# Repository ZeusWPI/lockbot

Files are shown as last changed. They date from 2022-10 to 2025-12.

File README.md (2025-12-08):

# Lockbot

Lockbot is a robot attached to our door that makes it possible for trusted members who don't have a key to open the door. It consists of a servo motor, two gears, a potentiometer and an Arduino Uno + ethernet shield.

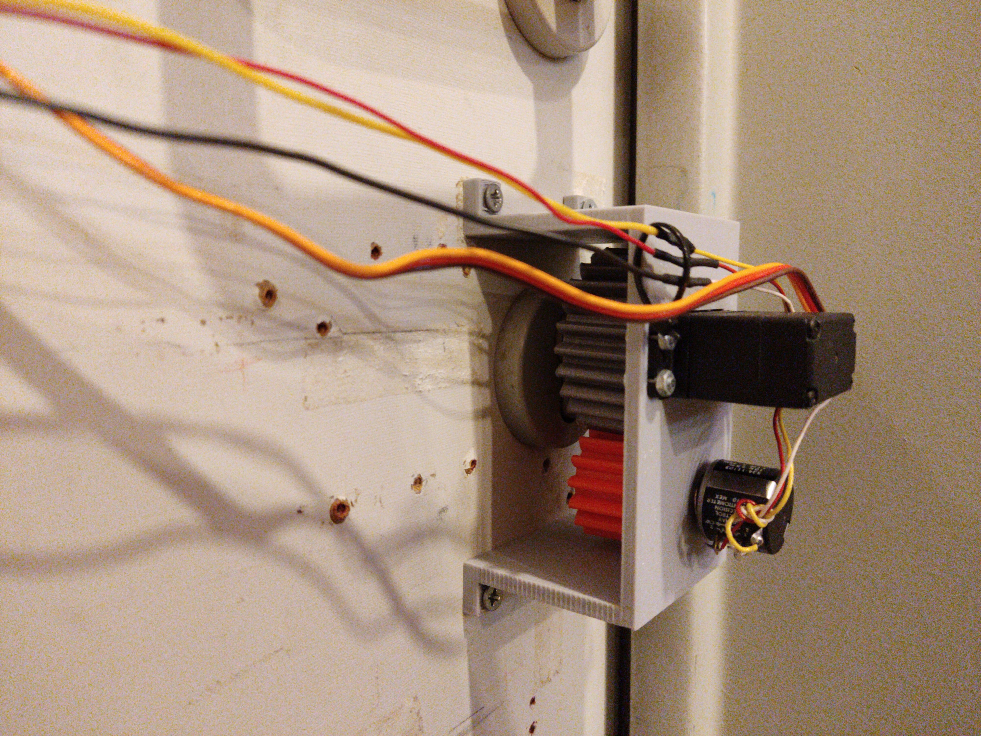
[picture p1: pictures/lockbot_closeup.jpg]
A closeup of just the motor and gears


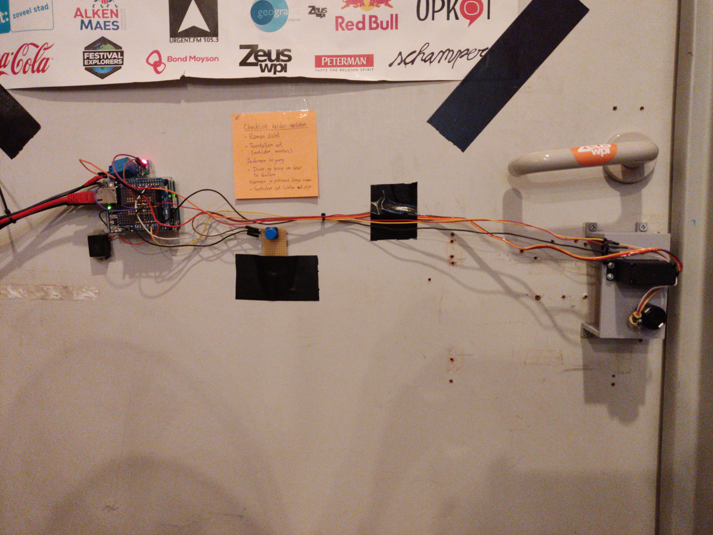
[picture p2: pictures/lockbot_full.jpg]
Global picture of lockbot


## Microcontroller build instructions

Requires the `platformio` cli tool, follow [these instructions](https://docs.platformio.org/en/latest/core/installation/methods/installer-script.html) to install it.

Next, in [arduino/src](arduino/src), copy `tokens.h.example` to `tokens.h` and edit them if necessary.

Finally, in [arduino](arduino), build and flash using the following:
```sh
. ~/.platformio/penv/bin/activate # Might depend on platform
pio run -t clean
pio run
pio run -t upload -t monitor
```

## 3D-print instructions

1. Install OpenSCAD
2. To print each lockbot part, open `printfile.scad` in OpenSCAD, uncomment the part you want to print, render it, export as STL then 3D print it. The big gear should be printed with 5 perimeter walls and solid infill, so it can handle the forces.

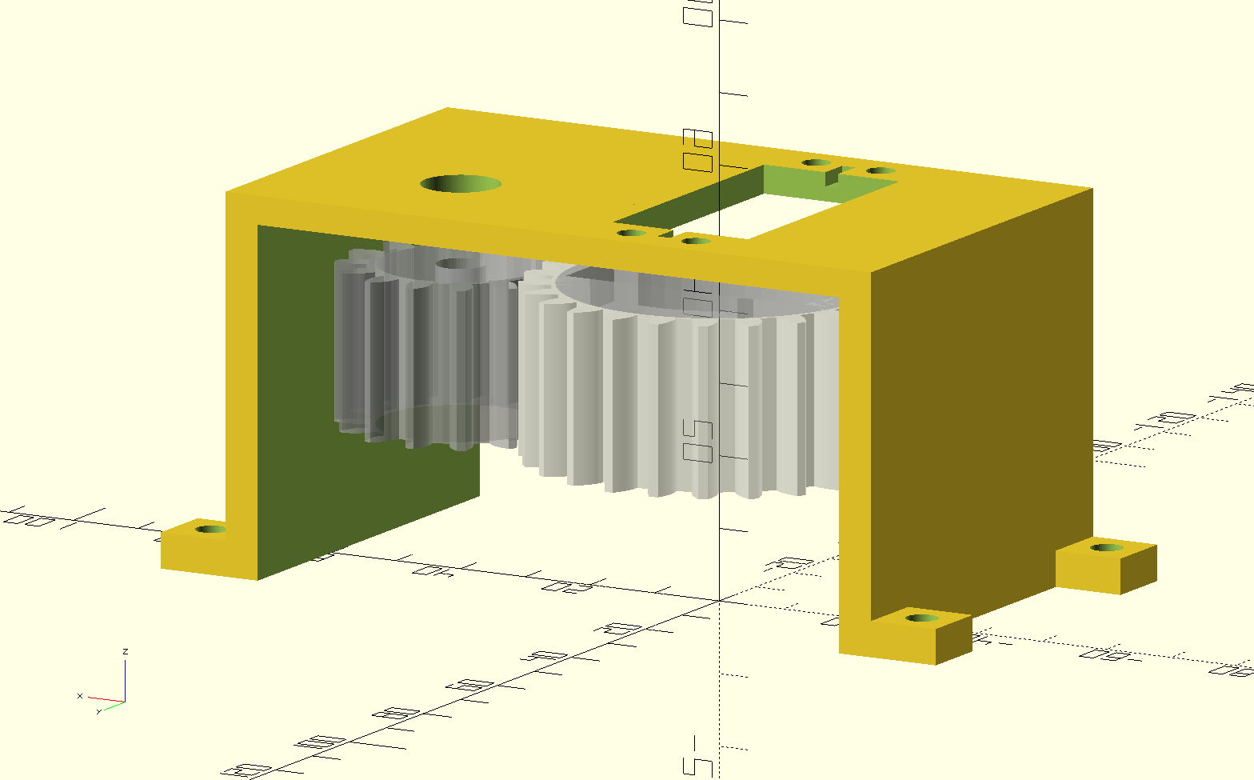
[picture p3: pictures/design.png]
The two gears and support used in lockbot Gears


The NFC plate that holds the NFC cards is also included in this repository, see `nfc_plate.scad`. There's spacers for the motor in `spacer.scad`, this will need to be modified for different motors.

## Components

- Arduino Uno + power supply for Arduino Uno (5V USB)
- Servo motor: TD-8130MG 360° Servo Motor - 30kg/cm + separate power supply for the servo motor
- Relay (also connected to motor power supply)
- Ethernet shield
- Buzzer
- Button
- 10k multiturn potentiometer

See [lockbot.cpp](arduino/src/lockbot.cpp) for how to connect these components together.

Make sure that when turning the lock, the multiturn potentiometer does not go out of bounds
(overturning it WILL break it).

## Calibration

Before lockbot can be used, you'll need to calibrate 4 points using `client.py <subcommand>`

- `calibrate_open_pos`: the position you'd like lockbot to go to when opening the door
- `calibrate_open_bnd`: the last position where you consider the door as 'open'
- `calibrate_close_bnd`: the first position where you consider the door as 'locked'
- `calibrate_close_pos`: the position you'd like lockbot to go to when closing the door

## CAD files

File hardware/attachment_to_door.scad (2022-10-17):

// This is the module that attaches the motor to the door
// all units in mm

include <lockbot.scad>;

$fn=100;


module ccube(size = [1,1,1], center = false)
{
  sz = (len(size) == 3)?size:[size,size,size];
  if (len(center) == 1)
    cube(size, center);
  else
    translate([center[0]?-sz[0]/2:0,center[1]?-sz[1]/2:0,center[2]?-sz[2]/2:0])
    cube(size);
}


motor_holder_to_door_distance = 53;
gear_to_door_distance=45;

motor_holder_hole_distance_horizontal = 10;
motor_holder_hole_diameter = 4;
motor_holder_hole_distance_vertical = 49.5;
motor_case_vertical = 40;
motor_case_horizontal = 20;
distance_shaft_to_case = 30; // or 10, from other side
cut=100;

module foot() {
    difference() {
        ccube([10, 10, 5], center=[1, 1, 0]);
        union() {
            translate([0, 0, -1]) cylinder(d=4.5, h=cut);
        }
    }
    
    
}

module_vertical=60;
module_horizontal=100;

module attachment_to_door() {
    difference() {
    translate([15, -10, 0]) union() {

        ccube([module_horizontal, module_vertical, motor_holder_to_door_distance], center=[true, true, false]);
        translate([-module_horizontal/2-5, -module_vertical/2+5, 0]) foot();
        translate([module_horizontal/2+5, -module_vertical/2+5, 0]) foot();
        translate([-module_horizontal/2-5, module_vertical/2-5, 0]) foot();
        translate([module_horizontal/2+5, module_vertical/2-5, 0]) foot();
    }
    union() {
        translate([0, 0, -1]) {
            translate([15, -10, 0]) ccube([module_horizontal-10, module_vertical+10, gear_to_door_distance+4+1], center=[1, 1, 0]);
        }
        translate([gear_distance, 0, -1]) cylinder(d=11, h=cut);
        translate([0, -10, -1]) ccube([motor_case_horizontal+1, motor_case_vertical+1, cut], center=[1, 1, 0]);
        translate([motor_holder_hole_distance_horizontal/2, -(distance_shaft_to_case+5), -1]) cylinder(d=4, h=cut);
        translate([-motor_holder_hole_distance_horizontal/2, -(distance_shaft_to_case+5), -1]) cylinder(d=4, h=cut);
        translate([motor_holder_hole_distance_horizontal/2, (motor_case_vertical-distance_shaft_to_case)+5, -1]) cylinder(d=4, h=cut);
        translate([-motor_holder_hole_distance_horizontal/2, (motor_case_vertical-distance_shaft_to_case)+5, -1]) cylinder(d=4, h=cut);
        translate([0, -10, motor_holder_to_door_distance-2]) ccube([2, 50, cut], center=[1, 1, 0]);
    }
}
% translate([0, 0, 45-25]) main_gear();
% translate([gear_distance, 0, 45-25]) small_gear();
}

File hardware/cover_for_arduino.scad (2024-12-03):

$fn=100;

heatset_height = 5.8 + 0.2;
heatset_diam = 3.9 + 0.1;

m3_clearance=3.6;

wall=10;

cut=100;

inner_width = 85;
inner_length = 150;
inner_height = 45;

cover_wall = 4;

module ccube(size = [1,1,1], center = false)
{
  sz = (len(size) == 3)?size:[size,size,size];
  if (len(center) == 1)
    cube(size, center);
  else
    translate([center[0]?-sz[0]/2:0,center[1]?-sz[1]/2:0,center[2]?-sz[2]/2:0])
    cube(size);
}

module door_mount() {
    difference() {
        cube([wall+inner_length+wall, wall+inner_width+wall, wall]);
        union() {
            translate([wall, wall, -1]) cube([inner_length, inner_width, cut]);
            translate([-1, (2*wall+inner_width)/2 - 20/2, 1]) cube([50, 20, cut]);
            translate([inner_length, wall, -1]) cube([50, 20, 8+1]);

            for (dx = [0, wall+inner_length]) {
                for (dy = [0, wall+inner_width]) {
                    translate([wall/2+dx, wall/2+dy, 0]) union() {
                        translate([0, 0, wall-heatset_height]) cylinder(d=heatset_diam, h=10);
                        translate([0, 0, -1]) cylinder(d=m3_clearance, h=wall-heatset_height+1);
                    }
                }
            }

            for (dx = [20, wall+inner_length-20]) {
                for (dy = [0, wall+inner_width]) {
                    translate([wall/2+dx, wall/2+dy, 0]) union() {
                        translate([0, 0, -0.5-1]) cylinder(h=6, r=4.1/2);
                        translate([0, 0, 5.1-1]) cylinder(h=6, r1=4.1/2, r2=(4.1 + 0.76*6)/2);
                    }
                }
            }
        }
    }
}

module cover() {
    difference() {
        union() {
            cube([wall+inner_length+wall, wall+inner_width+wall, 2]);
            translate([wall-cover_wall, wall-cover_wall,0]) cube([cover_wall+inner_length+cover_wall, cover_wall+inner_width+cover_wall, inner_height+cover_wall]);
        }
        union() {
            translate([wall, wall, -1]) cube([inner_length, inner_width, inner_height+1]);
            translate([-1, (2*wall+inner_width)/2 - 20/2, -1]) cube([wall+1+0.5, 20, 35-wall+1]);
            for (dx = [0, wall+inner_length]) {
                for (dy = [0, wall+inner_width]) {
                    translate([wall/2+dx, wall/2+dy, 0]) union() {
                        translate([0, 0, 2]) cylinder(d=10, h=cut);
                        translate([0, 0, -1]) cylinder(d=3.6, h=cut);
                    }
                }
            }
        }
    }
    

    %union() {
        for (dx = [0, wall+inner_length]) {
                for (dy = [0, wall+inner_width]) {
                    translate([wall/2+dx, wall/2+dy, 0]) union() {
                        color([0.5, 0.5, 0.5]) translate([0, 0, 0]) cylinder(d=6, h=10);
                    }
                }
        }
    }
    
}

door_mount();
translate([0, 0, wall+1]) cover();

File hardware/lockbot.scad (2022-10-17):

use <gears.scad>;

$fn=200;
width_back=33 + 1;
width_front=31 + 2;
height_front=14.5 + 2;
depth=17.8;


big_gear_teeth=25;
small_gear_teeth=15;
modul=2;
gear_distance=(big_gear_teeth+small_gear_teeth)*modul/2;



// knob can turn 1.5 turns in total, let's make that 2
// potentiometer turns 10 turns

potentiometer_shaft_diameter=6.35 + 0.5;
potentiometer_shaft_depth=7;
potentiometer_groove_width=0.6;
potentiometer_groove_depth=1;


// 13 clearance from width_back to bar keeping door in place

chest_bottom=7 + 2;

module centered_cube(size = [1,1,1], center = false)
{
  sz = (len(size) == 3)?size:[size,size,size];
  if (len(center) == 1)
    cube(size, center);
  else
    translate([center[0]?-sz[0]/2:0,center[1]?-sz[1]/2:0,center[2]?-sz[2]/2:0])
    cube(size);
}


module knob() {
  linear_extrude(height = depth, convexity = 10, scale=width_front/width_back)
  polygon(points=[[-chest_bottom/2,-width_front/2],[chest_bottom/2,-width_front/2],[height_front/2,0],[chest_bottom/2,width_front/2],[-chest_bottom/2,width_front/2], [-height_front/2,0]]);
}

module main_gear() {
  difference() {
    union() {
      spur_gear(modul, big_gear_teeth, depth+6, width_front+2, optimized=false);
      cylinder(r=width_back/2+5, h=depth+6);
    }

    union() {
      scale([1.3, 1.2, 1]) translate([0, 0, -0.01]) knob();
      translate([0, 0, depth-0.02]) centered_cube(size=[40, 13, 20], center=[1, 1, 0]);
      translate([-13, 0, 0]) cylinder(r=0.7, h=100);
      translate([13, 0, 0]) cylinder(r=0.7, h=100);
    }
  }

}

module small_gear() {
  extra_height=15;
  spur_gear(modul, small_gear_teeth, potentiometer_shaft_depth+extra_height, potentiometer_shaft_diameter);
  cylinder(r=5, h=extra_height-potentiometer_groove_depth);
  color([1, 0.5, 0]) intersection() {
    cylinder(r=5, h=extra_height);
    translate([0, 0, extra_height-potentiometer_groove_depth]) centered_cube([10, potentiometer_groove_width, potentiometer_groove_depth], center=[true, true, false]);
  }
}

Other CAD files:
hardware/nfc_plate.scad
hardware/gears.scad
hardware/printfile.scad
hardware/spacers.scad

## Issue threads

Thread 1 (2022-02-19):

Use hot-melt insert with set screw for small gear

redfast00, 2022-02-19:
The small gear is rotationally constained to the potentiometer with a small groove, but can still move up and down the potentiometer. For now, this is 'fixed' with some hot glue, but that's not an ideal solution since it might come loose.

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

Reprinting the gead and adding a hole on the side on the gear for a hot-melt threaded insert would allow us to put in a set-screw that keeps the gear secured on the potentiometer.

redfast00, 2022-02-19:
Alternatively, you can replace the hot-melt insert with just a regular nut inside of the gear, but this might be tricky to put in place and won't work if the size of the nut is bigger than the size of the shaft of the potentiometer

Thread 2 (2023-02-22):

Implement better fail-safe fallback

redfast00, 2023-02-22:
Als de deur nu gesloten wordt, gebeurt het soms dat de motor niet verdergaat, en dan panickt de deur (panicken gebeurt wanneer er kracht wordt gezet op de motor, maar de deur niet voldoende beweegt).

Een betere approach zou zijn om nog proberen in de andere richting te draaien, om dan vanaf een mogelijks betere positie te kunnen starten.

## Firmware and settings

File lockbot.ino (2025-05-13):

// Compile for Arduino Uno

#define ARDUINOJSON_USE_LONG_LONG 1
#include <PWMServo.h>    // install from Arduino libraries manager (version 2.1.0)
#include <Ethernet.h>    // install from Arduino libraries manager (version 2.0.2)
#include "./toneAC2/toneAC2.h"
#include "./toneAC2/toneAC2.cpp"
#include <SPI.h>         // built-in
#include <EEPROM.h>      // built-in
#include "./tokens.h"
#include "./sha256/sha256.h"
#include "./sha256/sha256.cpp"
#include "./util.h"


#define OPEN_POS_ADDRESS 0
#define CLOSED_POS_ADDRESS 8
#define OPEN_BOUND_ADDRESS 12
#define CLOSED_BOUND_ADDRESS 16

#define ENABLE_BOMBPLANTSOUND true

// Connect wiper pin of 10k potentiometer to A0, the other pins to VCC and ground
#define POTENTIOMETER_PIN A0

// Connect IN pin of relay to pin 3, VCC pin to the motor power supply 5V, ground to ground
// common to the motor power supply 5V cable, NO (normal open) to the 5V cable of the motor
#define RELAY_PIN 3

// Connect one leg of the button to 5, the other to ground
#define BUTTON_PIN 5

// Leave this pin unconnected (or alternatively, connect a short length of wire to the pin and leave unconnected)
// This is used to collect randomness via ADC noise
#define UNCONNECTED_RANDOM_PIN A1

// SERVO_PIN_A = 9
// Connect the data pin of the servo motor to pin 9, ground to ground. VCC should already be connected to NO of the relay

// toneAC buzzer pins
#define BUZZER_1 4
#define BUZZER_2 7

#define ANALOG_PRECISION 4

EthernetServer server(80);
EthernetClient client;

PWMServo door;

Debounced delayedLockButton;

int last_value_turnassist;
uint32_t last_turnassist_move = 0;

char* hmac_header_name = "HMAC: ";

char generated_random[32+1] = {};
bool received_challenge_response = false;


bool getHMACHeader(EthernetClient* client, uint8_t* buf) {
  if (!client->find(hmac_header_name)) return false;

  char octet[3] = {0};
  for (int i = 0; i < 32; i++) {
    int first = client->read();
    if (first < 0 || first == '\n') return false;
    int second = client->read();
    if (second < 0 || second == '\n') return false;
    octet[0] = (char) first;
    octet[1] = (char) second;
    *buf = strtol(octet, 0, 16);
    buf++;
  }
  return true;
}

void give400(EthernetClient* client, const char* message) {
  client->println(F("HTTP/1.1 400"));
  client->println(F("Connection: close"));
  client->println();
  client->print(message);
  client->flush();
  client->stop();
}

uint64_t current_command_counter = 0;

// Process incoming HTTP request
bool handleIncoming(String *command)
{
  client = server.available();
  if (!client) return false;
  uint8_t hmac_message[32] = {0};
  if (!getHMACHeader(&client, hmac_message)) {
    give400(&client, "no_hmac");
    // Not enough memory :/
    // sendMattermoreData("no_hmac", "attack", 0);
    return false;
  }
  // skip rest of headers
  client.find("\r\n\r\n");
  int bytes_read = 0;
  uint8_t body_buffer[128+1] = {0};
  // allow reading body of up to 128 bytes (should be enough)
  while (bytes_read < 128 && client.available()) {
    body_buffer[bytes_read] = client.read();
    bytes_read++;
  }

  if (client.available()) {
    give400(&client, "LENGTH");
    // Not enough memory :/
    // sendMattermoreData("too_long", "attack", 0);
    return false;
  }
  Sha256Class hmac_generator;
  hmac_generator.initHmac(DOWN_COMMAND_KEY, strlen((const char*) DOWN_COMMAND_KEY));
  Serial.println((char*) body_buffer);
  hmac_generator.write(body_buffer, bytes_read);
  uint8_t* hmac_calculated = hmac_generator.resultHmac();
  if (memcmp(hmac_calculated, hmac_message, 32) != 0) {
    give400(&client, "wrong_hmac");
    // Not enough memory :/
    // sendMattermoreData("wrong_hmac", "attack", 0);
    return false;
  }

  // parse body
  uint64_t received_ctr = 0;
  const char* body_str = body_buffer;
  while (*body_str != ';' && *body_str != 0) {
    received_ctr *= 10;
    received_ctr += *body_str - '0';
    body_str++;
  }
  if (received_ctr <= current_command_counter) {
    give400(&client, "REPLAY");
    // Not enough memory :/
    // sendMattermoreData("replay", "attack", 0);
    return false;
  }
  current_command_counter = received_ctr;
  body_str++; // skip ';'
  *command += body_str;

  client.println("HTTP/1.1 200");
  client.println("Content-Lenght: 1");
  client.println();
  client.print((int) getLockStatus());
  client.flush();
  client.stop();
  return true;
}

// Sends the processed commands back to mattermore to send to the channel
bool sendMattermoreData(const char* command, const char* reason, int value)
{
  EthernetClient requestclient;
  Serial.print("Sending to mattermore: ");
  Serial.println(reason);
  if (requestclient.connect(MATTERMORE_SERVER_HOST, MATTERMORE_SERVER_PORT))
  {
    String msg = String("cmd="+String(command)+"&why="+String(reason)+"&val="+String(value));
    Serial.println(msg);
    Sha256Class hmac_generator;
    hmac_generator.initHmac(UP_COMMAND_KEY, strlen((const char*) UP_COMMAND_KEY));
    hmac_generator.write(msg.c_str(), msg.length());
    uint8_t* hmac_calculated = hmac_generator.resultHmac();
    char hmac_header_hex[32*2+1] = {0};
    char* hmac_header_build = hmac_header_hex;
    for (int i = 0; i < 32; i++) {
      sprintf(hmac_header_build, "%.2X", hmac_calculated[i]);
      hmac_header_build += 2;
    }


    requestclient.println(F("POST /doorkeeper HTTP/1.1"));
    requestclient.print(F("Host: "));
    requestclient.println(MATTERMORE_SERVER_HOST);
    requestclient.print(hmac_header_name);
    requestclient.println(hmac_header_hex);
    requestclient.print(F("Content-Length: "));
    requestclient.println(msg.length());
    requestclient.println(F("Connection: close"));
    requestclient.println();
    requestclient.println(msg);
    requestclient.flush();
    requestclient.stop();
    return true;
  }
  Serial.println(F("Connecting failed"));
  requestclient.stop();
  return false;
}

// Maintain ethernet connection
void maintainEthernet()
{
  switch (Ethernet.maintain())
  {
    case 1:
    // Serial.println("Error: renewed fail");
    break;
    case 2:
    // Serial.println("Renewed success");
    break;
    case 3:
    // Serial.println("Error: rebind fail");
    break;
    case 4:
    // Serial.println("Rebind success");
    break;
    default:
    break;
  }
}

/*
Servo functions
94 ms is hold pos
> 94 -> open, CCW from the back
< 94 -> close, CW from the back
*/
void turnOpen()   {digitalWrite(RELAY_PIN, HIGH); door.write(10); Serial.println(F("Turning towards open"));}
void turnClose()  {digitalWrite(RELAY_PIN, HIGH); door.write(170); Serial.println(F("Turning towards close"));}
void turnHalt()   {digitalWrite(RELAY_PIN, LOW); door.write(94); Serial.println(F("Turning halt"));}

void turnDirection(bool directionIsOpen) {
  if (directionIsOpen) {
    turnOpen();
  } else {
    turnClose();
  }
}

#define MS_DIT 50
#define FREQ 600

void panic(const char* msg) {
  turnClose();

  uint32_t starttime = millis();
  while (millis() - starttime < 5000) {
    if (((millis() - starttime) / 250) % 2 == 0) {
      toneAC2(BUZZER_1, BUZZER_2, 300);
    } else {
      noToneAC2();
    }
  }

  turnHalt();
  sendMattermoreData(msg, "panic", getLockStatus());
  const char morse[] = ".--. .- -. .. -.-.";
  int index = 0;
  starttime = millis();
  bool interelement = false;
  while (true) {
    uint32_t time_passed = millis() - starttime;
    char current = morse[index];
    uint32_t duration;
    if (interelement) {
      duration = MS_DIT;
      noToneAC2();
    } else if (current == '.') {
      duration = MS_DIT;
      toneAC2(BUZZER_1, BUZZER_2, 800);
    } else if (current == '-') {
      duration = 3 * MS_DIT;
      toneAC2(BUZZER_1, BUZZER_2, 800);
    } else if (current == ' ') {
      duration = 2 * MS_DIT; // 3 - 1 because we already did interelement
      noToneAC2();
    } else if (current == 0) {
      duration = 5 * MS_DIT; // 7 - 2 because we already did interelement and will do interelement again
      noToneAC2();
    } else {
      duration = 10 * MS_DIT;
      toneAC2(BUZZER_1, BUZZER_2, 800);
    }
    if (time_passed > duration) {
      starttime = millis();
      if (interelement) {
        if (current == 0) {
          Serial.println(msg);
        }
        index = (index + 1) % (sizeof(morse));
      }
      interelement = !interelement;
    }
  }
}

void bringToState(int desired_value) {
  int open_value, closed_value;
  EEPROM.get(OPEN_POS_ADDRESS, open_value);
  EEPROM.get(CLOSED_POS_ADDRESS, closed_value);
  int current_value = analogRead(POTENTIOMETER_PIN);
  bool initial_to_desired_positive = (desired_value - current_value) >= 0;
  bool toward_open_is_positive = (open_value - closed_value) > 0;
  bool direction = initial_to_desired_positive == toward_open_is_positive;

  uint32_t last_move_check = millis();
  int last_check_value = current_value;
  int least_movement = abs(open_value - closed_value) / 20;

  turnDirection(direction);

  while (true) {
    current_value = analogRead(POTENTIOMETER_PIN);
    if (initial_to_desired_positive == (current_value > desired_value)) {
      turnHalt();
      break;
    }
    if (millis() - last_move_check > 1000) {
      if (initial_to_desired_positive == (last_check_value + (initial_to_desired_positive ? 1 : -1) * least_movement > current_value)) {
        panic("Passed turning deadline"); // this will never return
        return;
      } else {
        last_move_check = millis();
        last_check_value = current_value;
      }
    }
  }
  // Wait for the lock to end up in a stable position
  do {
    last_check_value = current_value;
    delay(500);
    current_value = analogRead(POTENTIOMETER_PIN);
  } while (abs((last_check_value - current_value)) > ANALOG_PRECISION);
  last_value_turnassist = analogRead(POTENTIOMETER_PIN);
}

void lockDoor()
{
  if (getLockStatus() == closed) return;
  int desired;
  EEPROM.get(CLOSED_POS_ADDRESS, desired);
  bringToState(desired);
}

void openDoor()
{
  if (getLockStatus() == open) return;
  int desired;
  EEPROM.get(OPEN_POS_ADDRESS, desired);
  bringToState(desired);
}

lock_status getLockStatus()
{
  int open_value, closed_value;
  EEPROM.get(OPEN_POS_ADDRESS, open_value);
  EEPROM.get(CLOSED_POS_ADDRESS, closed_value);
  int open_bound, closed_bound;
  EEPROM.get(OPEN_BOUND_ADDRESS, open_bound);
  EEPROM.get(CLOSED_BOUND_ADDRESS, closed_bound);
  bool toward_open_is_positive = (open_value - closed_value) > 0;

  int current_value = analogRead(POTENTIOMETER_PIN);
  if (toward_open_is_positive == (current_value > open_bound)) {
    return open;
  }
  if (toward_open_is_positive == (current_value < closed_bound)) {
    return closed;
  }
  return inbetween;
}

void delayedLock() {
  unsigned long start = millis();
  unsigned long next_change = millis() + 500;
  bool play = true;
  toneAC2(BUZZER_1, BUZZER_2, 800);
  while (millis() - start < 10000) {
    if (millis() > next_change) {
      if (play) {
        toneAC2(BUZZER_1, BUZZER_2, 800);
      } else {
        noToneAC2();
      }
      play = !play;
      next_change = millis() + (start + 10000 - millis()) / 20;
    }
  }
  noToneAC2();
  lockDoor();
}

void handleCommand(const char* command, const char* reason, int* value)
{
  int current_value = analogRead(POTENTIOMETER_PIN);
  *value = current_value;
  // TODO implement challenge/response here and only allow other commands once challenge/response succeeded
  //  this to prevent an attacker from tripping the breaker, thus making the Arduino (and the replay prevention counter) reset
  // The attacker can then replay an already sent packet they MITM'ed earlier.

  if (strcmp("open", command) == 0) {
    openDoor();
  } else if (strcmp("lock", command) == 0) {
    lockDoor();
  } else if (strcmp("delay", command) == 0) {
    if(ENABLE_BOMBPLANTSOUND) sendMattermoreData(command, "locking", *value); //play "bomb has been planted" if enabled
    delayedLock();
  } else if (strcmp("status", command) == 0) {
    *value = getLockStatus();
  } else if (strcmp("calibrate_open_pos", command) == 0) {
    EEPROM.put(OPEN_POS_ADDRESS, current_value);
  } else if (strcmp("calibrate_open_bnd", command) == 0) {
    EEPROM.put(OPEN_BOUND_ADDRESS, current_value);
  } else if (strcmp("calibrate_close_pos", command) == 0) {
    EEPROM.put(CLOSED_POS_ADDRESS, current_value);
  } else if (strcmp("calibrate_close_bnd", command) == 0) {
    EEPROM.put(CLOSED_BOUND_ADDRESS, current_value);
  } else {
    panic("Invalid command");
  }
  sendMattermoreData(command, reason, *value);
}

lock_status last_status;

void setup()
{
  pinMode(RELAY_PIN, OUTPUT);
  digitalWrite(RELAY_PIN, LOW);
  pinMode(BUTTON_PIN, INPUT_PULLUP);
  toneAC2(BUZZER_1, BUZZER_2, 500);
  last_value_turnassist = analogRead(POTENTIOMETER_PIN);
  Serial.begin(9600);
  Serial.println("Booting up ...");

  Serial.println("Initialising servo controller ...");
  // Config servo motor control pin, 500-2500 is for the 10kg/cm servo
  // SERVO_PIN_A = pin 9 see http://arduiniana.org/libraries/pwmservo/
  door.attach(SERVO_PIN_A);
  turnHalt();

  Serial.println("Initialising ethernet ...");

  byte mac[] = {0x00, 0x20, 0x91, 0x10, 0x00, 0x00};
  IPAddress ip(192, 168, 0, 5);
  IPAddress subnetMask(255, 255, 252, 0);
  IPAddress gateway(192, 168, 0, 1);
  Ethernet.begin(mac, ip, gateway, gateway, subnetMask);

  Serial.println("Starting webserver ...");
  server.begin();

  Serial.println("Doorkeeper: online");
  sendMattermoreData("up", "boot", getLockStatus());
  for (int i = 0; i < 32; i++) {
    generated_random[i] = 'A' + (analogRead(UNCONNECTED_RANDOM_PIN) % 26);
  }
  sendMattermoreData((char*) generated_random, "chal", getLockStatus());
  noToneAC2();
  last_status = getLockStatus();
}

void turnAssistLoop() {
  int current_value = analogRead(POTENTIOMETER_PIN);
  // don't assist after just having turned to prevent humans trying to get their key out activating turn assist again
  if (millis() - last_turnassist_move < 10000) {
    last_value_turnassist = current_value;
    return;
  }

  int open_value, closed_value;
  EEPROM.get(OPEN_POS_ADDRESS, open_value);
  EEPROM.get(CLOSED_POS_ADDRESS, closed_value);
  bool toward_open_is_positive = (open_value - closed_value) > 0;

  int turnassist_minimum = max(abs(open_value - closed_value) / 20, ANALOG_PRECISION);
  // Serial.print("minimum = ");
  // Serial.println(turnassist_minimum);
  // Serial.println(last_value_turnassist);
  Serial.println(current_value);

  if (toward_open_is_positive == (current_value > open_value)) {
    return; // no need to turnassist, we're after the open value
  }
  if (toward_open_is_positive == (current_value < closed_value)) {
    return; // no need to turnassist, we're before the closed value
  }
  if (abs(current_value - last_value_turnassist) > turnassist_minimum) {
    Serial.print("Deciding to move based on value = ");
    Serial.print(current_value);
    Serial.print(" compared to ");
    Serial.println(last_value_turnassist);
    bool going_toward_open = (toward_open_is_positive == ((current_value - last_value_turnassist) > 0));
    int value;
    handleCommand(going_toward_open ? "open" : "lock", "turnassist", &value);
    last_turnassist_move = millis();
  }
}
uint32_t lastprint = 0;
uint32_t last_change_state = 0;

void loop()
{
  maintainEthernet();
  delayedLockButton.loop(digitalRead(BUTTON_PIN) == LOW);

  String rxCommand;
  int value = 0;
  if (handleIncoming(&rxCommand)) {
    handleCommand(rxCommand.c_str(), "mattermore", &value);
  }

  if (delayedLockButton.get_and_reset_press_count() > 0) {
    Serial.println("delayedClose");
    handleCommand("delay", "delaybutton", &value);
    delay(100);
  }
  // disabled until we get a 10k potentiometer
  // turnAssistLoop();
  if (millis() - lastprint > 1000) {
    Serial.println(analogRead(POTENTIOMETER_PIN));
    lastprint = millis();
  }

  lock_status new_status = getLockStatus();
  if (new_status != inbetween && new_status != last_status) {
    last_status = new_status;
    sendMattermoreData("change", "state", last_status);
  }
}

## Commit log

2021-11-15 Make small gear longer
    [lockbot.scad]
2022-02-07 Widen hole for thumb-latch
    [lockbot.scad]
2022-02-08 More detailed README
    [lockbot.scad]
2022-02-08 Add active mechanical buzzer
    [lockbot.ino]
2022-10-17 Document some more
    [attachment_to_door.scad, lockbot.scad, nfc_plate.scad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]
2022-11-03 Add protective cover for Arduino
    [cover_for_arduino.scad]
2023-03-01 Used a different servo motor
    [spacers.scad]
2023-03-27 Change back to piezo buzzer
    [lockbot.ino]
2024-12-03 Design more robust cover for lockbot
    [cover_for_arduino.scad]
2025-02-18 remove try statement because it doesn't exist in arduino lmao
    [lockbot.ino]
2025-12-08 dev(arduino): Use platformio for building.
    Move all source code to arduino/.
    Lock dependencies.
    Build flags: Remove -fpermissive, add -Wall, add -Wextra.
    Fix implicit declaration and cast errors.
    Update build instructions in README.md.
    [lockbot.cpp]
2025-12-08 style(arduino): Add and apply editorconfig.
2025-12-08 style(arduino): Add and apply .clang-format.
2025-12-08 dev(arduino): Remove unused SPI dependency.
2025-12-08 fix(arduino): Typo in Content-Length.
    [lockbot.cpp]
2025-12-08 chore(arduino): Move arduino-specific gitignore to `arduino/`.
2025-12-08 style(arduino): Use .hpp instead of .h and format.
2025-12-09 fix(arduino): Always recover after panicking (#2).
    When a panic occurs, the door is always closed just fine.
    Keep the current 5 second continued turning, but after that proceed as normal.
    Handle the invalid_command panic as just a warning, similar to the attacks.
    [lockbot.cpp]
